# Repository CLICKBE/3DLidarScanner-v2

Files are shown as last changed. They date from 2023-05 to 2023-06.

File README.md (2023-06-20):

# 3D LiDAR scanner v2 - With stepper motors, Arduino UNO and Arduino CNC Shield v3

This repository demonstrates a homemade 3D LiDAR scanner made out of a [Benewake TF-Mini LiDAR sensor](https://www.gotronic.fr/art-capteur-de-distance-lidar-tf-mini-27615.htm) and 2 stepper motors NEMA17 ([17HS4401](https://boutique.semageek.com/fr/1443-moteur-pas-a-pas-17hs4401-12v-nema17-200-pasrev-17a-3005762453528.html) and [Casun 42SHD0001-24B](http://www.all-electronics-online.com/china-828911685/42shd0001-24b-high-torque-12v-dc-nema-17-stepper-motor-for-3d-printer.html)). This scanner can produce 3D cloud point of spaces.
The LiDAR sensor is fixed on one stepper arm with the help of a 3D printed bracket. This stepper is fixed to the second stepper arm through another bracket. 

|scannerLidar-stepper | scan3D-exemple|
| :---: | :---: |
| The 3D LiDAR scanner| Example of 3D visualisation of the scanning |

## Files in the repository
- src/main.cpp: file to be uploaded to the Arduino Uno board;
- src/stepperScanner-serial2CSV.py: script to save scan data into a CSV file;
- 3D_support: folder containing different 3D models for supports made; 
- fritzing: [Fritzing](https://fritzing.org/) file used to draw the connection picture.

## Elements to build the scanner

### Parts
- Benewake TF-Mini Lidar sensor: [https://www.gotronic.fr/art-capteur-de-distance-lidar-tf-mini-27615.htm](https://www.gotronic.fr/art-capteur-de-distance-lidar-tf-mini-27615.htm); 
- Arduino CNC Shield v3: [https://blog.protoneer.co.nz/arduino-cnc-shield/](https://blog.protoneer.co.nz/arduino-cnc-shield/);
- Horizontal stepper: [17HS4401](https://boutique.semageek.com/fr/1443-moteur-pas-a-pas-17hs4401-12v-nema17-200-pasrev-17a-3005762453528.html), NEMA 17, 12V, 1.7A, 200 step/rev;
- Vertical stepper: [Casun 42SHD0001-24B](http://www.all-electronics-online.com/china-828911685/42shd0001-24b-high-torque-12v-dc-nema-17-stepper-motor-for-3d-printer.html), NEMA17, 12V, 0.4A, 200 step/rev;
- External power: 12V, 2A;
- (optional) Maker Beam aluminium profiles and hardware or other.

### Connection

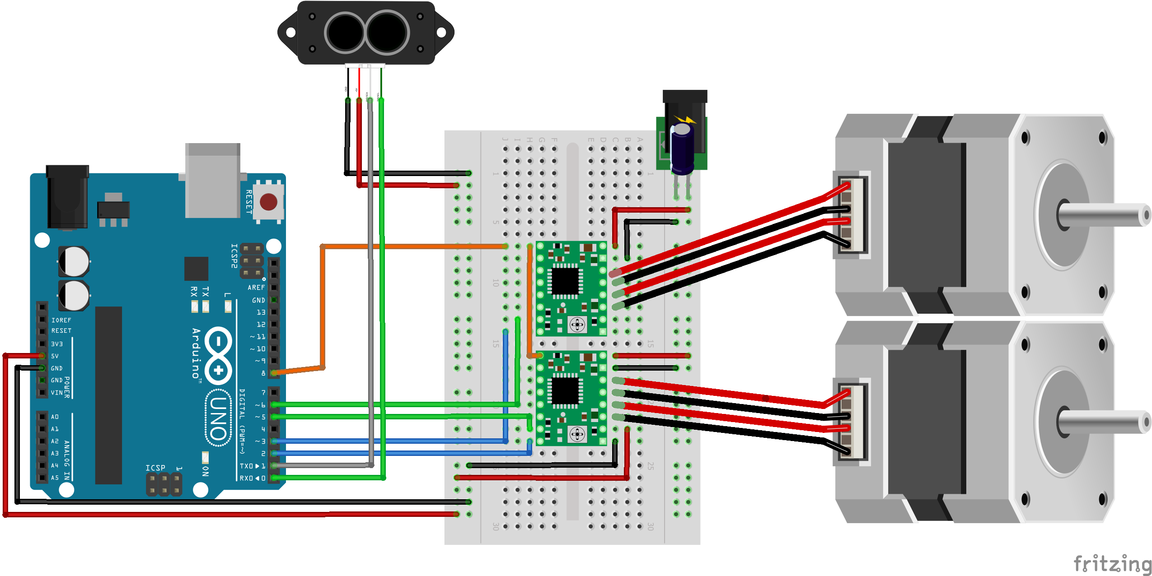
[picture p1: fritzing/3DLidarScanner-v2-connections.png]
3DLidarScanner with stepper connections


Note that this diagram replicates the use of the Arduino CNC Shield v3 by using the same pin to connect the two drivers.

### 3D models
To make this prototype we printed supports (that you can see on the picture above): one to connect the two steppers together and the other one to support the LiDAR senor and connect it to one of the NEMA 17 stepper.

If you need to edit the 3d models you can use the [Freecad](https://www.freecad.org/) files (*.FCStd).

More 3D models for steppers and LiDAR sensors can be found in a specific repo : [https://github.com/CLICKBE/3DModelsFor3dPrinters](https://github.com/CLICKBE/3DModelsFor3dPrinters).

## Using the 3D LiDAR scanner v2

### Code

This code has been developed with VSCode and PlatformIO backend. This repo therefore reproduced the folder structure used in such project. Once you opened VSCode, open PlatformIO home page and hit Open Project button. Then, select the folder of the repository.

If you don't know anything about VSCode and PlatformIO, here's a link to set you up : [https://platformio.org/install/ide?install=vscode](https://platformio.org/install/ide?install=vscode).

### Library needed : 
- TFMPlus: [https://github.com/budryerson/TFMini-Plus](https://github.com/budryerson/TFMini-Plus). The library is not included in this git repository but is referenced in the [platformio.ini](https://github.com/CLICKBE/3DLidarScanner-v2/blob/main/platformio.ini) file and therefore should directly be downloaded by PlatformIO extension of VSCode when building the code.
- SoftwareSerial: included in Arduino framework

### Scanner serial protocol
Once the Arduino script is uploaded and running onto the Arduino Uno board, the scanner can be control through serial protocol at 115200 bauds. The following commands are available : 

- s : perform 2D scan;
- y : perform 1D scan (vertical);
- i : display scanner setup info;
- v : followed by an integer value sets the vertical step (e.g. `v 1`);
- h : followed by an integer value sets the horizontal step (e.g. `h 1`);
- p : scan reboot.
   
Once the scan is launched (through s or y), it performs the XYZ coordinates conversion and ouputs all of the data through serial port in the following manner : 

`x y z h_idx v_idx distance`

With : 
- x: x coordinate in 3D space;
- y: y coordinate in 3D space;
- z: z coordinate in 3D space;
- h_idx: horizontal index of the scan;
- v_idx: vertical index of the scan;
- distance: data coming from TF-Mini-s LiDAR sensor.

### Parsing data to CSV files
The `stepperScanner-serial2CSV.py` python script establishes serial communication with the Arduino Uno used for the 3D Lidar scanner. Once the script is launched, it stores incoming data (`x y z h_idx v_idx distance`) into a csv file.

Usage is as follows (one can use `python stepperScaneer-serial2CSV.py -h` to check on the available option arguments) : 

`python stepperScanner-serial2CSV.py -p YOUR_ARDUINO_SERIAL_PORT -b 115200 -f /your/filepath/to/the/data/storage.csv`

Once the script is launched, the serial commands described above can be used to control the scanner.

## 3D Visualization of the scan

To perform a quick 3D visualization based on the serial data you can use the Processing script developed by Dana Peters : [LidarScanner.pde](https://drive.google.com/file/d/1D5wfzA8i0Pzh4qe-1skmpnqmhrvaq9d3/view?usp=drive_web) who also developed a [3D LiDAR scanner](https://www.qcontinuum.org/lidar-scanner).

In order to use this script, you will need free [Processing](https://processing.org/) software.

In order to send commands from this Processing sketch to the scanner, you can modified the `keyPressed()` function of the code by adding the following `else` condition to the `if, else if` statements that are present :  
```java
else 
{
    try 
    {
      serial.write( key );
      println( "Sending command to scanner" );
    }
    catch (Exception e)
    {
      println( "Exception " + e );
    }
}
```

## License
 © 2022 – CLICK - Université de Mons

3D LiDAR scanner v2 - with stepper motors – CLICK - UMONS (Loïc Reboursière, Maxime Vander Goten, Sami Yunus) is free software: you can redistribute it and/or modify it under the terms of the Apache License Version 2.0. This program is distributed in the hope that it will be useful, but WITHOUT ANY WARRANTY; without even the implied warranty of MERCHANTABILITY or FITNESS FOR A PARTICULAR PURPOSE.  See the Apache License Version 2.0 for more details.
You should have received a copy of the Apache License Version 2.0 along with this program.  If not, see http://www.apache.org/licenses/
Each use of this software must be attributed to University of MONS – CLICK (Loïc Reboursière, Maxime Vander Goten, Sami Yunus).
Any other additional authorizations may be asked to avre@umons.ac.be.

## Legal Notices
This work was produced as part of the FEDER Digistorm project, co-financed by the European Union and the Wallonia Region.

Logo FEDER-FSE

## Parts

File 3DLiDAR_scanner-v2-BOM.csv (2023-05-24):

Reference | Type | Quantity | Manufacturer | Link | Info
Arduino Uno | Micrcontroller | 1 | Arduino | https://store.arduino.cc/products/arduino-uno-rev3
Arduino CNC Shield | Daughter card | 1 | Protoneer | https://blog.protoneer.co.nz/arduino-cnc-shield/
NEMA 17 | Stepper Motor | 2 | Nema | https://www.gotronic.fr/cat-moteurs-pas-a-pas-1093.htm
Stepper holder | Support | 1 | Click
TF-Mini-S | LiDAR | 1 | Beneware | https://www.gotronic.fr/art-capteur-de-distance-lidar-tf-mini-27615.htm
TF-Mini-S holder | Support | 1 | Click

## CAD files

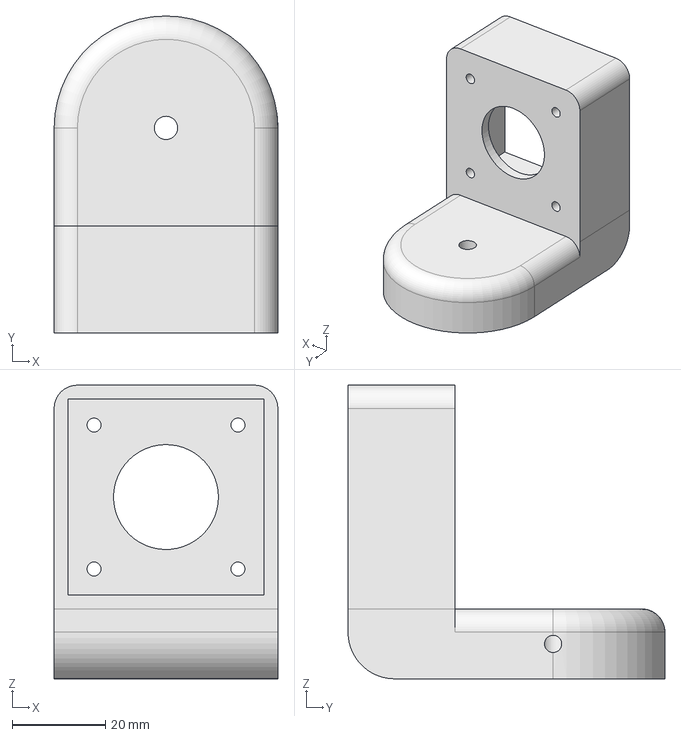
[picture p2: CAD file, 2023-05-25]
3D_support/3DSupport-NEMA17_17HS4401-NEMA17_Casun_42SHD0001_24B.FCStd
48.0 x 68.0 x 63.0 mm

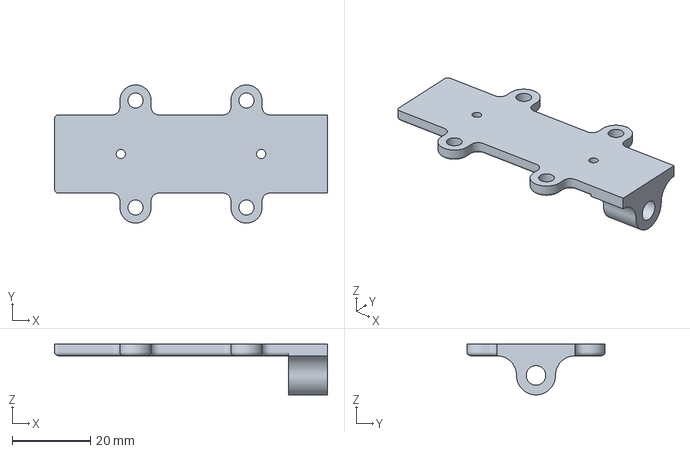
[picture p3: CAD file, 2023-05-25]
3D_support/3DSupport-NEMA17_17HS4401-TFMiniS-Body.3mf
70.0 x 35.4 x 13.0 mm

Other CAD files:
3D_support/3DSupport-NEMA17_17HS4401-NEMA17_Casun_42SHD0001_24B-Body.3mf
3D_support/3DSupport-NEMA17_17HS4401-TFMiniS.FCStd

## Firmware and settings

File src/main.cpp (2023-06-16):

/**
 * 
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
 * @copyright Copyright (c) 2023
 * 
 */

#include <Arduino.h>
#include <SoftwareSerial.h>
// To use with TFMini-Plus library, https://github.com/budryerson/TFMini-Plus/tree/master
// along with getData( int16_t &dist, int16_t &flux, int16_t &temp) function
#include "TFMPlus.h"
// To use with TFMini Library, https://github.com/opensensinglab/tfmini/blob/master/src/TFMini.h
// Along with getDistance() function
//#include "TFMini.h"
//TFMini tfmini;

TFMPlus tfmini;
SoftwareSerial SerialTFMini(10, 11);  //define software serial port name as Serial1 and define pin2 as RX & pin3 as TX

// Arduino CNC Shield connections
// https://blog.protoneer.co.nz/arduino-cnc-shield/
#define MOTOR_X_STEP 2
#define MOTOR_Y_STEP 3
#define MOTOR_Z_STEP 4
#define MOTOR_X_DIRECTION 5
#define MOTOR_Y_DIRECTION 6
#define MOTOR_Z_DIRECTION 7
#define STEPPER_ENABLE 8

#define TICKS_PER_REVOLUTION 200 // Specification of the NEMA 17 type stepper motor
#define SUBDIVISION  1. / 8. // Chosen through a CNC Shield card jumper

#define SERIAL_SPEED 115200
#define TFMINI_SERIAL_SPEED 115200

float total_nb_of_steps = TICKS_PER_REVOLUTION / SUBDIVISION;
float degree_per_step = 360 / total_nb_of_steps; 

int vertical_nb_of_steps = total_nb_of_steps / 5;// Vertical rotation of 90°
int horizontal_nb_of_steps = total_nb_of_steps / 12; // Horizontal rotation of 30° - factor of 9 for 40°
int vertical_offset = 2;
int horizontal_offset = 10;

int posx=0;
int posy=0;

// Functions declaration
/***
 * Move the horizontal motor by a certain amount of steps
 * Arguments : 
 *  steps (long) : number of steps to move the motor.
 * Return :
 *  void
 */
void xmove( long steps );

/***
 * Move the vertical motor by a certain amount of steps
 * Arguments : 
 *  steps (long) : number of steps to move the motor.
 * Return :
 *  void
 */
void ymove( long steps );

/***
 * Move a specific motor by a certain amount of steps
 * Arguments : 
 *  steps (long) : number of steps to move the motor.
 *  motor_direction_pin (int) : the pin of the Arduino connected to the direction of the stepper motor.
 *  motor_step_pin (int) : the pin of the Arduino connected to the step of the stepper motor.
 * Return :
 *  void
 */
void moveStepper( long steps, int motor_direction_pin, int motor_step_pin );

/***
 * Display info from the scanner setup : (nb of steps (vertical and horizontal), ticks per revolution, total number of steps, subdivision  
 * Arguments : 
 *  None
 * Return :
 *  void
 */ 
void displayInfo();

/***
 * Send throught serial horizontal position, vertical position, distance and their converted XYZ coordinates.
 * The message is as follows : 
 *    scanning_horizontal_position scanning_vertical_position distance X Y Z
 * Arguments : 
 *  None
 * Return :
 *  void
 */
void displayCoordinates();

/***
 * Convert horiz_step_idx, vert_step_idx and distance to (x, y, z) coordinates.
 * Computation comes from : https://github.com/bitluni/3DScannerESP8266
 * And https://www.youtube.com/watch?v=vwUGPjQ_5t4
 * Arguments : 
 *  *x (float) : the float pointer to the x coordinates
 *  *y (float) : the float pointer to the y coordinates
 *  *z (float) : the float pointer to the z coordinates
 *  distance (int16_t) : distance retrieved by LiDAR sensor
 *  hAngleDegree (int) : horizontal angle in degree of the pantilt sweeping
 *  vAngleDegree (int) : vertical angle in degree of the pantilt sweeping
 * Return :
 *  void
 */ 
void computeXYZ( float *x, float *y, float *z, int16_t distance, int hAngleDegree, int vAngleDegree );


/* ----------------------------- ACTUAL PROGRAM ----------------------------- */
void setup() {
  
  //motor X
  pinMode( MOTOR_X_STEP, OUTPUT );
  digitalWrite( MOTOR_X_STEP,LOW );
  
  pinMode( MOTOR_X_DIRECTION, OUTPUT );
  digitalWrite( MOTOR_X_DIRECTION, LOW );

  //motor Y  
  pinMode( MOTOR_Y_STEP, OUTPUT );
  digitalWrite( MOTOR_Y_STEP, LOW );
  
  pinMode( MOTOR_Y_DIRECTION, OUTPUT );
  digitalWrite( MOTOR_Y_DIRECTION, LOW );
  
  // motor Z
  pinMode( MOTOR_Z_STEP, OUTPUT );
  digitalWrite( MOTOR_Z_STEP,LOW );
  
  pinMode( MOTOR_Z_DIRECTION, OUTPUT );
  digitalWrite( MOTOR_Z_DIRECTION, LOW );
  
  //motor enable
  pinMode( STEPPER_ENABLE, OUTPUT );
  digitalWrite( STEPPER_ENABLE, LOW );
  
  Serial.begin( SERIAL_SPEED );         //set bit rate of serial port connecting Arduino with computer

  SerialTFMini.begin( TFMINI_SERIAL_SPEED );    //Initialize the data rate for the SoftwareSerial port
  tfmini.begin( &SerialTFMini );            //Initialize the TF Mini sensor}

  // For now the steppers are manually zeroed. 
  // The zero pointface the ground (vertically) and is paralleled to the back of the structure (horizontal)
  // The total nb of horizontal steps is share out around this manually set horizontal zero 

}

int16_t distance = 0;    // Distance to object in centimeters
int16_t tfFlux = 0;    // Strength or quality of return signal
int16_t tfTemp = 0;    // Internal temperature of Lidar sensor chip
float x = -1., y = -1., z = -1.;
bool scan = true;

void loop() {
  
  while( Serial.available() == 0 ){}

  char inbyte=Serial.read();
  //Serial.println( "Command " + String( inbyte ) );
  switch ( inbyte ){
  
  //-------------------------------
  // To be remove for final git
  //case 117: //u
  //  zmove(10);
  //  posz=posz+10;
    //Serial.print(posx);
    //Serial.write(9);
    //Serial.println(posy);
  //break;
  
  // To be remove for final git
  //case 100: //d
  //  zmove(-10);
  //  posz=posz-10;
    //Serial.print(posx);
    //Serial.write(9);
    //Serial.println(posy);
  //break;
  //------------------- 
   case 112: //p to allow scan reboot
    scan = true;
    break;

  case 115: //s for 2D scan
    
    // "Init" x axis position
    // Step motor must be positionned manually to the center 
    xmove( -horizontal_nb_of_steps / 2 );

    while(Serial.available()==0){
      //Serial.println( "scanning" );
      int16_t distance = 0;
      //int16_t strength = 0;
      
      // For use of TFMPlus library
      tfmini.getData( distance, tfFlux, tfTemp); // For use of TFMini library : distance = getDistance();

      while ( !distance && scan )
      {
        //Serial.println( "No distance" );

        // For use of TFMPlus library
        tfmini.getData( distance, tfFlux, tfTemp ); // For use of TFMini library : distance = getDistance();
        if (distance){
          ymove( vertical_offset );
          //moveStepper( vertical_offset, )
          posy = posy + vertical_offset;
          computeXYZ( &x, &y, &z, distance, posx * degree_per_step, posy * degree_per_step );
          delay(10);

          displayCoordinates();

          if ( posy >= vertical_nb_of_steps ) { ymove( -vertical_nb_of_steps ); posy = 0; xmove( horizontal_offset ); posx = posx + horizontal_offset;} // déplacement vertical ()
          if ( posx >= horizontal_nb_of_steps ) { xmove( -horizontal_nb_of_steps ); posx = 0; scan = false; Serial.println( "stop" ); break;} // 

        }
      }
    }
  Serial.println( "stop" );
  break;

  case 121: //y for 1D scan
    
    while(Serial.available()==0){
      //Serial.println( "scanning" );
      int16_t distance = 0;
      //int strength = 0;

      // For use of TFMPlus library
      tfmini.getData( distance, tfFlux, tfTemp); // For use of TFMini library : distance = getDistance();

      while ( !distance && scan )
      {

        // For use of TFMPlus library
        tfmini.getData( distance, tfFlux, tfTemp );// For use of TFMini library : distance = getDistance();
        if (distance){
          //Serial.println( distance );
          // ymove( vertical_offset );
          ymove( vertical_offset );
          posy = posy + vertical_offset;
          computeXYZ( &x, &y, &z, distance, posx * degree_per_step, posy * degree_per_step );
          delay(10);

          displayCoordinates();

          if ( posy >= vertical_nb_of_steps ) {
            scan = false;
            Serial.println( "stop" );
            break;
          }

        }
      }
    }
  Serial.println( "end" );
  break;


  case 105 : // i to display info from the scanner setup
    displayInfo();
    Serial.println( "end" );
    break;

  case 118 : // v to set vertical offset (the command must be followed by an int)
    inbyte = Serial.read();
    vertical_offset = Serial.parseInt();
    Serial.println( "---- Modifying vertical offset, new value : " + String( vertical_offset ) );
    Serial.println( "end" );
    //displayInfo();
    break;

  case 104 : // h to set horizontal offset (the command must be followed by an int)
    inbyte = Serial.read();
    horizontal_offset = Serial.parseInt();
    Serial.println( "---- Modifying horizontal offset, new value : " + String( horizontal_offset ) );
    Serial.println( "end" );
    
    break;
  }

}


/* ---------------------------- FUNCTIONS' IMPLEMENTATIONS -----------------------------*/
void xmove( long steps )
{
  moveStepper( steps, MOTOR_X_DIRECTION, MOTOR_X_STEP );
}

void ymove( long steps )
{
   moveStepper( steps, MOTOR_Y_DIRECTION, MOTOR_Y_STEP );
}


void moveStepper( long steps, int motor_direction_pin, int motor_step_pin )
{
  if ( steps < 0 )
  {
    digitalWrite( motor_direction_pin, HIGH );
  }
  else
  {
    digitalWrite( motor_direction_pin, LOW );
  }
  
  for( long i = 0 ; i < abs( steps ) ; i++ ) 
  {
    digitalWrite( motor_step_pin, HIGH );
    delay( 5 );
    digitalWrite( motor_step_pin, LOW );
    delay( 5 );
  } 
}

void displayCoordinates()
{
  Serial.print( posx * degree_per_step );
  Serial.write( 9 );
  Serial.print( posy * degree_per_step );
  Serial.write( 9 );
  Serial.print(distance);
  Serial.write(9);
  Serial.print( x );
  Serial.write( 9 );
  Serial.print( y );
  Serial.write( 9 );
  Serial.println( z );
}

void displayInfo()
{
  Serial.println( "vertical_nb_of_steps " + String( vertical_nb_of_steps ) );
  Serial.println( "horizontal_nb_of_steps " + String( horizontal_nb_of_steps ) );
  Serial.println( "ticks_per_revolution " + String( TICKS_PER_REVOLUTION ) );
  Serial.println( "subdivision " + String( SUBDIVISION ) );
  Serial.println( "total_nb_of_steps " + String( total_nb_of_steps ) );
  Serial.println( "degree_per_step " + String( degree_per_step ) ); 
  Serial.println( "Vertical offset (in steps) : " + String( vertical_offset ) );
  Serial.println( "Horizontal offset (in steps) : " + String( horizontal_offset ) );
  Serial.println( "Vertical precision (in degree) : " + String( degree_per_step * vertical_offset ) );
  Serial.println( "Horizontal precision (in degree) : " + String( degree_per_step * horizontal_offset ) );
}

void computeXYZ( float *x, float *y, float *z, int16_t distance, int hAngleDegree, int vAngleDegree ) 
{

//  float yawf = hAngleDegree * M_PI / 180;
//  float pitchf = vAngleDegree * M_PI / 180;

  float pitchf = hAngleDegree * M_PI / 180;
  float yawf = vAngleDegree * M_PI / 180;


//  float yawf   = hAngleDegree;
//  float pitchf = vAngleDegree;

  //Serial.println(yawf);
  //Serial.println(pitchf);

  // *x = -sin( yawf ) * distance * cos( pitchf );
  // *y = cos( yawf ) * distance * cos( pitchf );
  // *z = distance * sin( pitchf );

  *x = distance * -sin( yawf ) * cos( pitchf );
  *y = distance * sin( yawf ) * sin( pitchf );
  *z = distance * cos( pitchf );

  //Serial.println( " Computing xyz from angles and distances : " 
  //                    + String( *x ) + " " 
  //                    + String( *y ) + " "
  //                    + String( *z ) 
  //                    + " -- point indexes "
  //                    + hAngleDegree + " " 
  //                    + vAngleDegree 
  //              );

}

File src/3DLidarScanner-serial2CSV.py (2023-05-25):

'''
#
# 
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
'''
 
# Connect the 3D Arduino-based LiDAR scanner performing the scan and launch this file.
# Use : 
#   python stepperScanner-serial2CSV.py --port the_port_of_connected_arduino_board --baudrate 115200
# 
# Once the serial communication is established, you can send any serial commands the scanner responds to :
#    - s : perform 2D scan
#    - y : perform 1D scan (vertical)
#    - i : display scanner setup info
#    - v : followed by an integer value sets the vertical step (e.g. `v 1`)
#    - h : followed by an integer value sets the horizontal step (e.g. `h 1`)
#    - p : scan reboot
#

import csv
from time import sleep

import serial
import argparse
import os, sys

def checkFileAndIncrement( folder_path, pattern ) :
    '''
    Count files of a specific folder with the same pattern.
    Arguments :
        folder_path : Path of the folder to investigate.
        pattern : Pattern to look for in files
    Return :
        Number of existing files. 0 means that none have been found.
    '''

    nb_of_existing_files = 0

    if folder_path == '' : folder_path = '.'

    for path in os.listdir( folder_path ) :
        if( pattern in path ):
            nb_of_existing_files += 1

    return nb_of_existing_files

def main (args) :

    filename = args.file
    ## TOCHECK : if it does what it's supposed to
    folder_path = os.path.dirname( filename )
    if folder_path == '' : folder_path = '.'    
    filename = os.path.join( folder_path, filename )
    
    if( os.path.isfile( filename ) ) :
        print( 'ERROR : Filename ' + filename + ' already exists, please enter a different filename.' )   
        sys.exit( 0 )
    else : 
        print( 'File doesn\'t exist')

    dataSerie = serial.Serial( port = args.port, baudrate = args.baudrate)
    print( '--- Connecting to port : ' + args.port + ' at ' + str( args.baudrate )  +' bauds' )

    listG = []
    nb_of_scan = 0

    ## Double while True loops need to be tested
    while True :
        data = input()
        #print( data )
        dataSerie.write( str.encode( data ) )
        
        if( data == 's' or data == 'y' ) :          

            while True:
                # sleep(0.1)

                mesure = dataSerie.readline().strip()
                mesureUtf = mesure.decode("utf-8")
                mesure1 = mesureUtf.split()

                print(mesure1)

                if mesureUtf == "end":

                    with open( filename, 'w' ) as f :
                        writer = csv.writer( f )
                        print( len( listG ) )
                        writer.writerows( listG )
                        break
                else: ## TODO : add all elements not just xYZ and then during parsing put them in the right dict keys
                    #listG.append( [ mesure1[ 6 ], mesure1[ 7 ], mesure1[ 8 ] + ";"] )
                    listG.append( mesureUtf )

        ## TOCHECK : do other serial commands send their feedback    
        else : ## you sent commands different from scanning commands
            data_raw = dataSerie.readline()
            if( data_raw == 'end' ) : 
                break 
            else : 
                print( data_raw )

        #else :
        #    while True:
        #        bytesToRead = dataSerie.inWaiting()
        #        print( dataSerie.read( bytesToRead ) )


if __name__ == "__main__":
    
    parser = argparse.ArgumentParser( description = 'Receive serial data from scanner and record it into a csv file.' )
    parser.add_argument( "-p", "--port",
                        help = "Serial port used to connect Arduino Uno USB",
                        type = str, default = "" )
    parser.add_argument( "-b", "--baudrate", 
                        help = "Speed of the serial communication (default is 115200)",
                        type = int, default = "115200" )
    parser.add_argument( "-f", "--filename", 
                        help = "Filename of the stored data (default is scanning_data.csv)",
                        type = str, default = "sanning_data.csv" )
    args = parser.parse_args()

    main( args )

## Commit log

2023-05-24 Fritzing update with TFmini-S fritzing model
    [3DLiDAR_scanner-v2-BOM.csv, 3DLidarScanner-v2.fzz]
2023-05-25 Addition - 3D models for stepper and Lidar supports
    [3DSupport-NEMA17_17HS4401-NEMA17_Casun_42SHD0001_24B-Body.3mf, 3DSupport-NEMA17_17HS4401-NEMA17_Casun_42SHD0001_24B.FCStd, 3DSupport-NEMA17_17HS4401-TFMiniS-Bo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]
2023-06-20 README minor updates
    [3DSupport-NEMA17_17HS4401-NEMA17_Casun_42SHD0001_24B-Body.3mf, 3DSupport-NEMA17_17HS4401-NEMA17_Casun_42SHD0001_24B.FCStd, 3DSupport-NEMA17_17HS4401-TFMiniS-Bo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]
